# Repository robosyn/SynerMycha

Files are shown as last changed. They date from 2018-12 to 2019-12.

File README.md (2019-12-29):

# SynerMycha

Projekt micromouse'a

## BOM

|Qty|Value|Device|Package|Parts|Description|
|---|-----|---|---|-----|---|
|3|Blue|LEDCHIP-LED0603|CHIP-LED0603|LED1,LED2,LED3||
|1|Red|LEDCHIPLED_0603|CHIPLED_0603|LED5||
|1||PINHD-1X2|1X02|POWER||
|1||PINHD-1X5|1X05|JP3||
|1||PINHD-2X3|2X03|JP1||
|1||SPDT-PTH-11.6X4.0MM|SPDT_PTH_11.6X4.0MM|S1||
|12|100nF|CAPACITOR_SMD_0603|C0603K|C5,C6,C16,C18,C19,C21,C23,C24,C27,C29,C31,C36||
|1|100nF|CPOL-EUSMCA|SMC_A|C1||
|7|10k|RESISTOR_SMD_0603|R0603|R8,R15,R16,R25,R26,R27,R28||
|1|16Mhz|CRYSTAL_SMALL";|Y1|12.0MHzCrystal||
|2|18pF|CAPACITOR_SMD_0603|C0603K|C8,C9||
|2|1k|R-EU_R0603|R0603|R13,R14||
|5|1k|RESISTOR_SMD_0603|R0603|R2,R3,R4,R5,R7||
|1|270|RESISTOR_SMD_0603|R0603|R6||
|7|2k2|RESISTOR_SMD_0603|R0603|R1,R9,R10,R11,R12,R23,R24||
|3|330|R-EU_R0402|R0402|R17,R18,R19||
|5|33uF|CPOL-EUC|PANASONIC_C|C3,C4,C7,C32,C34||
|2|ACS711|ACS712|SOIC127P600X175-8N|IC3,IC4||
|5|ADAFRUIT-VCNL4010|ADAFRUIT-VCNL4010|ADAFRUIT-VCNL4010|U$7,U$8,U$9,U$10,U$11||
|5|BC847|BC847|SOT23|T1,T2,T3,T4,T5||
|1|MICROMATCH-6|MICROMATCH-6|MICROMATCH-6|PROG-SWDIO||
|1|SPST-SMD-6.2MM|SPST-SMD-6.2MM|SPST_SMD_6.2MM|S2||
|2|AS5040|AS5040|AS5040|U$13,U$14||
|1|STM32F411RCT6|STM32F411RCT6|LQFP64|IC7||
|1|SWS004|SWS004|SMS-004|S3||
|2|TLE9201SG|TLE9201SG|PG-DSO-12-9|IC5,IC6||
|1|3V3|V_REG_317-DPACK|V-REG_DPACK|U2||
|2|N20BT06100:1|N20BT06100:1||||
|2|RW2isolarbotics|RW2isolarbotics||||
|2|300mAh|LiPol,Dualsky||||

## Linki do niektórych części

| Nazwa |kamami ID |cena (botland) |botland |electropark |tme |
| ---|:-----:|:---:|:---:|:---:|:--:|
| N20 BT06 | 562730 | 19.9zł| https://botland.com.pl/pl/silniki-micro-n20-seria-mp-medium-power/12545-silnik-n20-bt05-micro-501-625rpm-12v.html | tylko oryginalne |  tylko oryginalne pololu|
| RW2i solarbotics | 195993 | 24.9zł| https://botland.com.pl/pl/kola-z-oponami/24-kolo-solarbotics-rw2i-mocowane-wewnetrznie.html | chwilowo niedostpne | brak|
| lipol 300mah dualsky  | brak | 22.5zł| https://botland.com.pl/pl/akumulatory-li-pol/7876-pakiet-li-pol-dualsky-300mah-30c-2s-74v-6941047107403.html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 | wycofany | brak |
| stm32f411 | 233365 | brak  | chwilowo niedostępnu| 27.65 zł|https://www.tme.eu/pl/details/stm32f411rct6/mikrokontrolery-st/stmicroelectronics/|
| TLE9201 | brak | brak  | brak |13.93zł| https://www.tme.eu/pl/details/tle9201sgauma1/drivery-silnikowe-i-pwm/infineon-technologies/ |
| VCNL4010 | brak | 44zł  | https://botland.com.pl/pl/cyfrowe-czujniki-odleglosci/4969-adafruit-vcnl4010-czujnik-odleglosci-i-swiatla-20cm-i2c.html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| |tylko chip bez płytki na specjalne zamówienie |

~ oferta: 
~ 35zł https://www.elfadistrelec.pl/pl/czujnik-zblizeniowy-swiatla-vcnl4010-adafruit-466/p/30139237
plus ~50 za przesyłke
TLE9210 dostępne w labie

### CADLAB 

View this project on [CADLAB.io](https://cadlab.io/project/1503).

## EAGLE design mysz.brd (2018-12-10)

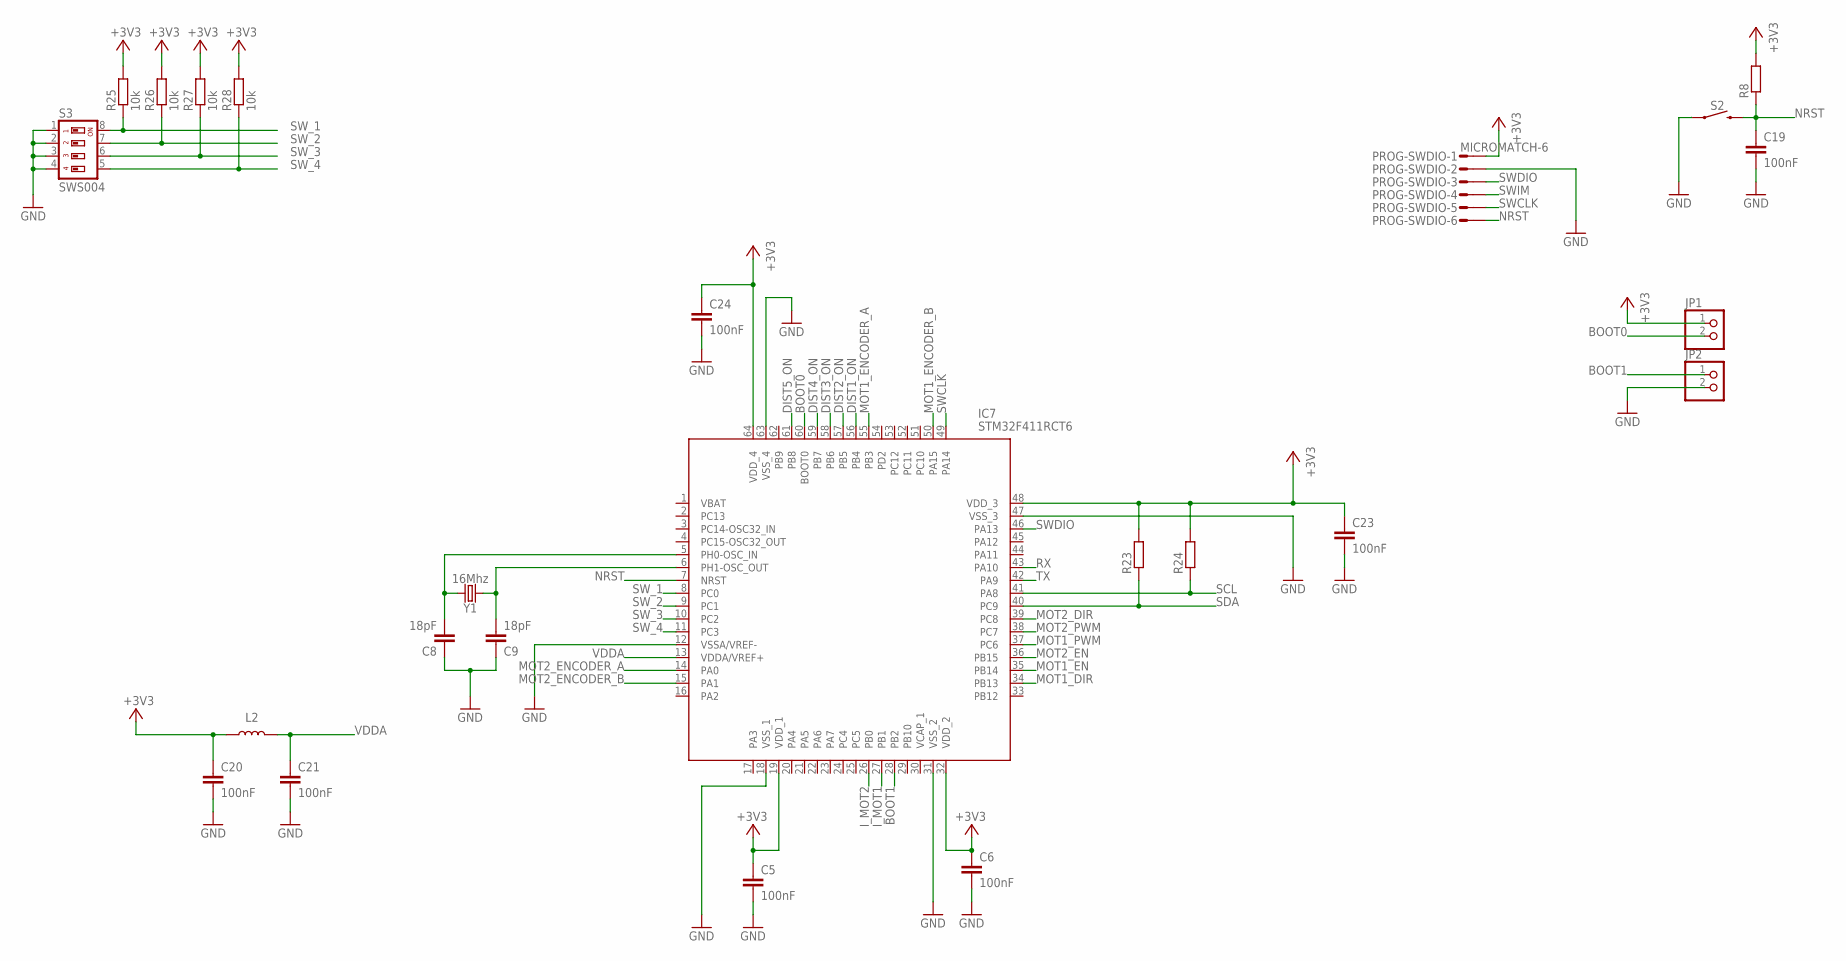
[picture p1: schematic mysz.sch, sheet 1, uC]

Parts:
C5, C6, C19, C20, C21, C23, C24: 100nF; C0603K
C8, C9: 18pF; C0603K
IC7: STM32F411RCT6; QFP50P1200X1200X160-64N
JP1, JP2: PINHD-1X2; 1X02
L2: INDUCTOR-0603; R0603
PROG-SWDIO: MICROMATCH-6
R8, R23, R24: RESISTOR_SMD_0603; R0603
R25, R26, R27, R28: 10k; R0603
S2: MOMENTARY-SWITCH-SPST-SMD-6.2MM_TALL; TACTILE_SWITCH_SMD_6.2MM_TALL
S3: SWS004; SMS-004
Y1: 16Mhz; CRYSTAL-SMD-5X3.2-4PAD

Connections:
+3V3: C5.1, C6.1, C20.1, C23.1, C24.1, IC7.19 (VDD_1), IC7.32 (VDD_2), IC7.48 (VDD_3), IC7.64 (VDD_4), JP1.1, L2.1, PROG-SWDIO.1, R8.2, R23.2, R24.2, R25.2, R26.2, R27.2, R28.2; also elsewhere on the board
BOOT0: IC7.60 (BOOT0), JP1.2
BOOT1: IC7.28 (PB2), JP2.1
DIST1_ON: IC7.56 (PB4); also elsewhere on the board
DIST2_ON: IC7.57 (PB5); also elsewhere on the board
DIST3_ON: IC7.58 (PB6); also elsewhere on the board
DIST4_ON: IC7.59 (PB7); also elsewhere on the board
DIST5_ON: IC7.61 (PB8); also elsewhere on the board
GND: C5.2, C6.2, C8.1, C9.1, C19.2, C20.2, C21.2, C23.2, C24.2, IC7.12 (VSSA/VREF-), IC7.18 (VSS_1), IC7.31 (VSS_2), IC7.47 (VSS_3), IC7.63 (VSS_4), JP2.2, PROG-SWDIO.2, S2.A1 (1), S2.A2 (1), S3.1, S3.2, S3.3, S3.4; also elsewhere on the board
I_MOT1: IC7.27 (PB1); also elsewhere on the board
I_MOT2: IC7.26 (PB0); also elsewhere on the board
MOT1_DIR: IC7.34 (PB13); also elsewhere on the board
MOT1_EN: IC7.35 (PB14); also elsewhere on the board
MOT1_ENCODER_A: IC7.55 (PB3); also elsewhere on the board
MOT1_ENCODER_B: IC7.50 (PA15); also elsewhere on the board
MOT1_PWM: IC7.37 (PC6); also elsewhere on the board
MOT2_DIR: IC7.39 (PC8); also elsewhere on the board
MOT2_EN: IC7.36 (PB15); also elsewhere on the board
MOT2_ENCODER_A: IC7.14 (PA0); also elsewhere on the board
MOT2_ENCODER_B: IC7.15 (PA1); also elsewhere on the board
MOT2_PWM: IC7.38 (PC7); also elsewhere on the board
NRST: C19.1, IC7.7 (NRST), PROG-SWDIO.6, R8.1, S2.B1 (2), S2.B2 (2)
RCC_OSC_IN: C8.2, IC7.5 (PH0-OSC_IN), Y1.3 (2)
RCC_OSC_OUT: C9.2, IC7.6 (PH1-OSC_OUT), Y1.1
RX: IC7.43 (PA10)
SCL: IC7.41 (PA8), R24.1; also elsewhere on the board
SDA: IC7.40 (PC9), R23.1; also elsewhere on the board
SWCLK: IC7.49 (PA14), PROG-SWDIO.5
SWDIO: IC7.46 (PA13), PROG-SWDIO.3
SWIM: PROG-SWDIO.4
SW_1: IC7.8 (PC0), R25.1, S3.8
SW_2: IC7.9 (PC1), R26.1, S3.7
SW_3: IC7.10 (PC2), R27.1, S3.6
SW_4: IC7.11 (PC3), R28.1, S3.5
TX: IC7.42 (PA9)
VDDA: C21.1, IC7.13 (VDDA/VREF+), L2.2

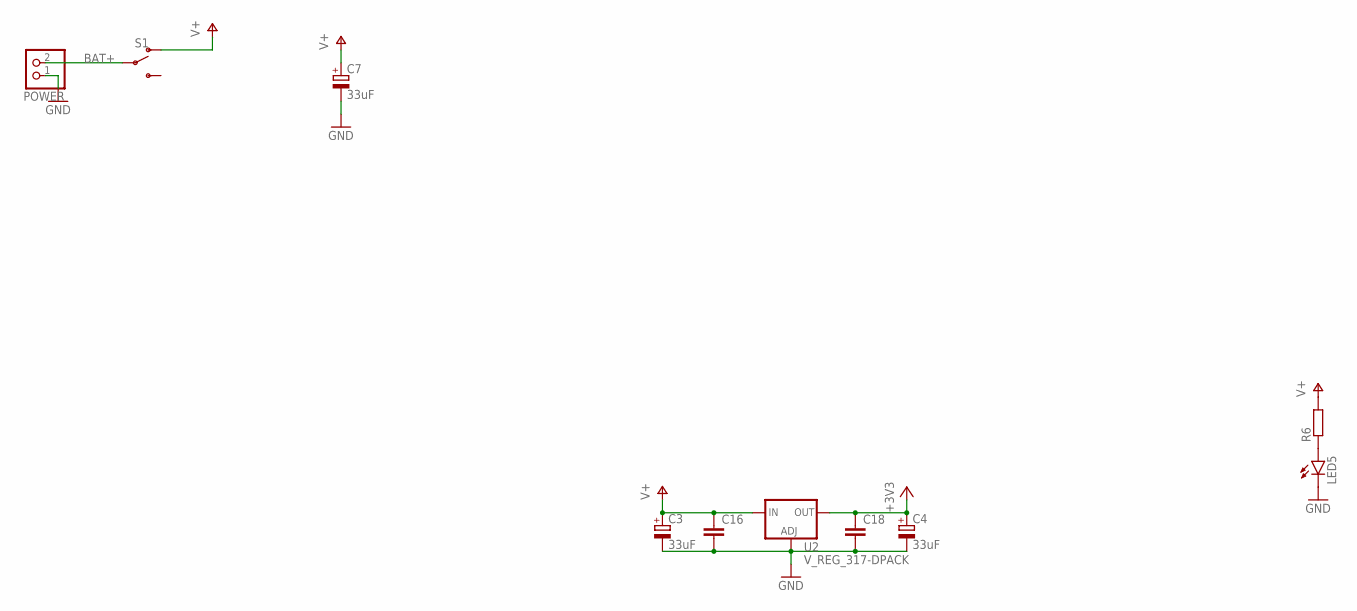
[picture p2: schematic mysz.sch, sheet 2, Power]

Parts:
C3, C4, C7: 33uF; PANASONIC_C
C16, C18: CAPACITOR_SMD_0603; C0603K
LED5: LEDCHIPLED_0603; CHIPLED_0603
POWER: PINHD-1X2; 1X02
R6: RESISTOR_SMD_0603; R0603
S1: SWITCH-SPDT-PTH-11.6X4.0MM; SWITCH_SPDT_PTH_11.6X4.0MM
U2: V_REG_317-DPACK; V-REG_DPACK

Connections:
+3V3: C4.+, C18.1, U2.4 (OUT); also elsewhere on the board
BAT+: POWER.2, S1.2
GND: C3.-, C4.-, C7.-, C16.2, C18.2, LED5.C, POWER.1, U2.1 (ADJ); also elsewhere on the board
unnamed: LED5.A, R6.1
V+: C3.+, C7.+, C16.1, R6.2, S1.1 (O), U2.3 (IN); also elsewhere on the board

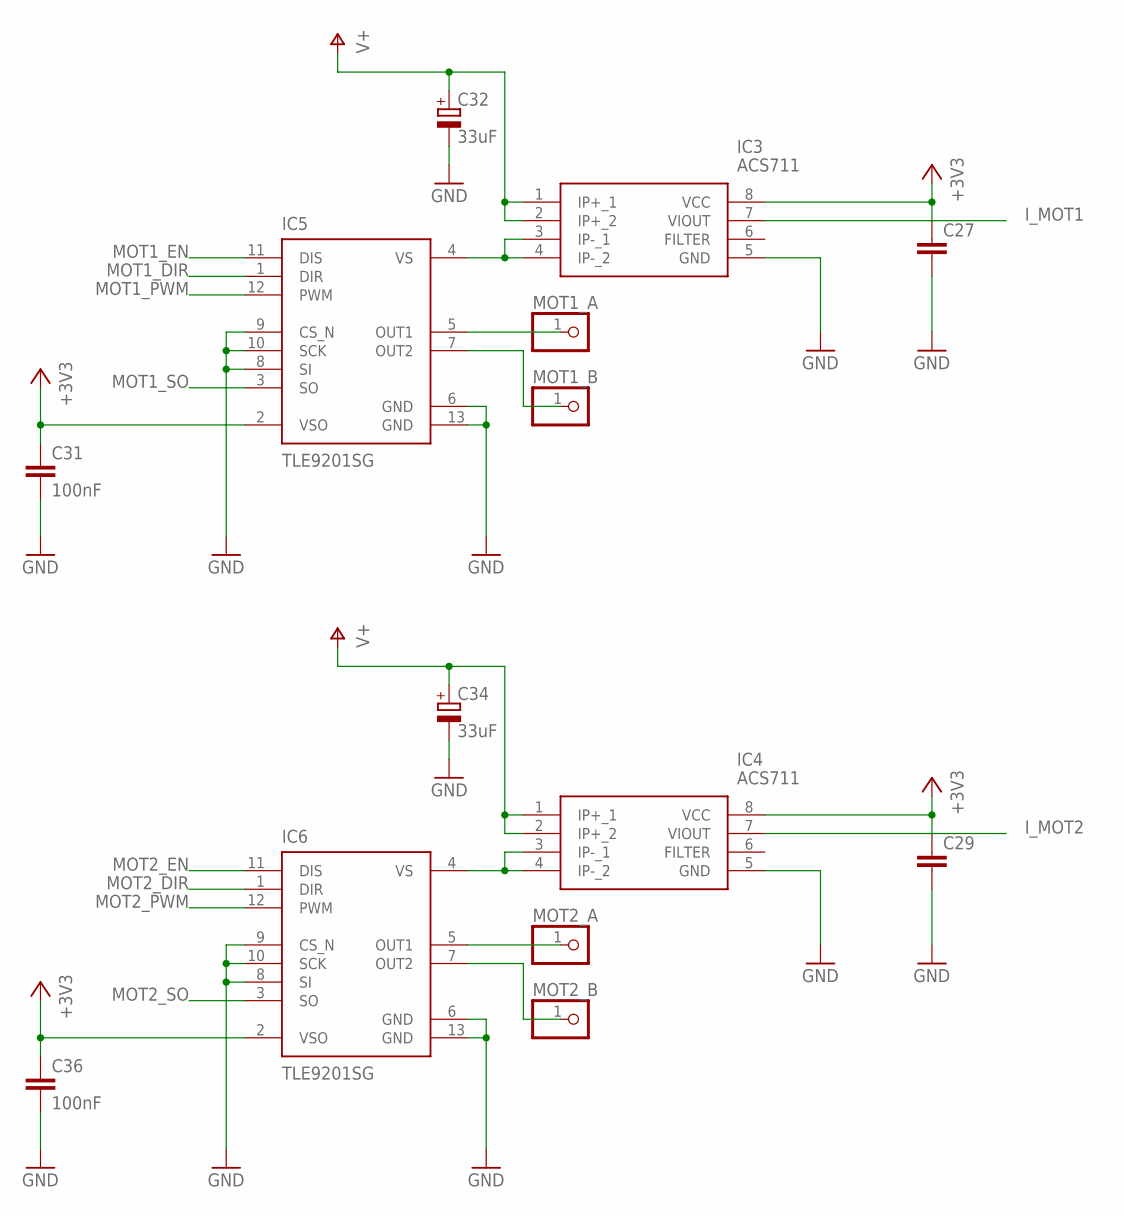
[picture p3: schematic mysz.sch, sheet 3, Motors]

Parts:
C27, C29: CAPACITOR_SMD_0603; C0603K
C31, C36: 100nF; C0603K
C32, C34: 33uF; PANASONIC_C
IC3, IC4: ACS711; SOIC127P600X175-8N
IC5, IC6: TLE9201SG; PG-DSO-12-9
MOT1_A, MOT1_B, MOT2_A, MOT2_B: PINHD-1X1; 1X01

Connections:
+3V3: C27.1, C29.1, C31.1, C36.1, IC3.8 (VCC), IC4.8 (VCC), IC5.2 (VSO), IC6.2 (VSO); also elsewhere on the board
GND: C27.2, C29.2, C31.2, C32.-, C34.-, C36.2, IC3.5 (GND), IC4.5 (GND), IC5.6 (GND), IC5.8 (SI), IC5.9 (CS_N), IC5.10 (SCK), IC5.13 (GND), IC6.6 (GND), IC6.8 (SI), IC6.9 (CS_N), IC6.10 (SCK), IC6.13 (GND); also elsewhere on the board
I_MOT1: IC3.7 (VIOUT); also elsewhere on the board
I_MOT2: IC4.7 (VIOUT); also elsewhere on the board
MOT1_A: IC5.5 (OUT1), MOT1_A.1
MOT1_B: IC5.7 (OUT2), MOT1_B.1
MOT1_DIR: IC5.1 (DIR); also elsewhere on the board
MOT1_EN: IC5.11 (DIS); also elsewhere on the board
MOT1_PWM: IC5.12 (PWM); also elsewhere on the board
MOT1_SO: IC5.3 (SO)
MOT1_VS: IC3.3 (IP-_1), IC3.4 (IP-_2), IC5.4 (VS)
MOT2_A: IC6.5 (OUT1), MOT2_A.1
MOT2_B: IC6.7 (OUT2), MOT2_B.1
MOT2_DIR: IC6.1 (DIR); also elsewhere on the board
MOT2_EN: IC6.11 (DIS); also elsewhere on the board
MOT2_PWM: IC6.12 (PWM); also elsewhere on the board
MOT2_SO: IC6.3 (SO)
MOT2_VS: IC4.3 (IP-_1), IC4.4 (IP-_2), IC6.4 (VS)
V+: C32.+, C34.+, IC3.1 (IP+_1), IC3.2 (IP+_2), IC4.1 (IP+_1), IC4.2 (IP+_2); also elsewhere on the board

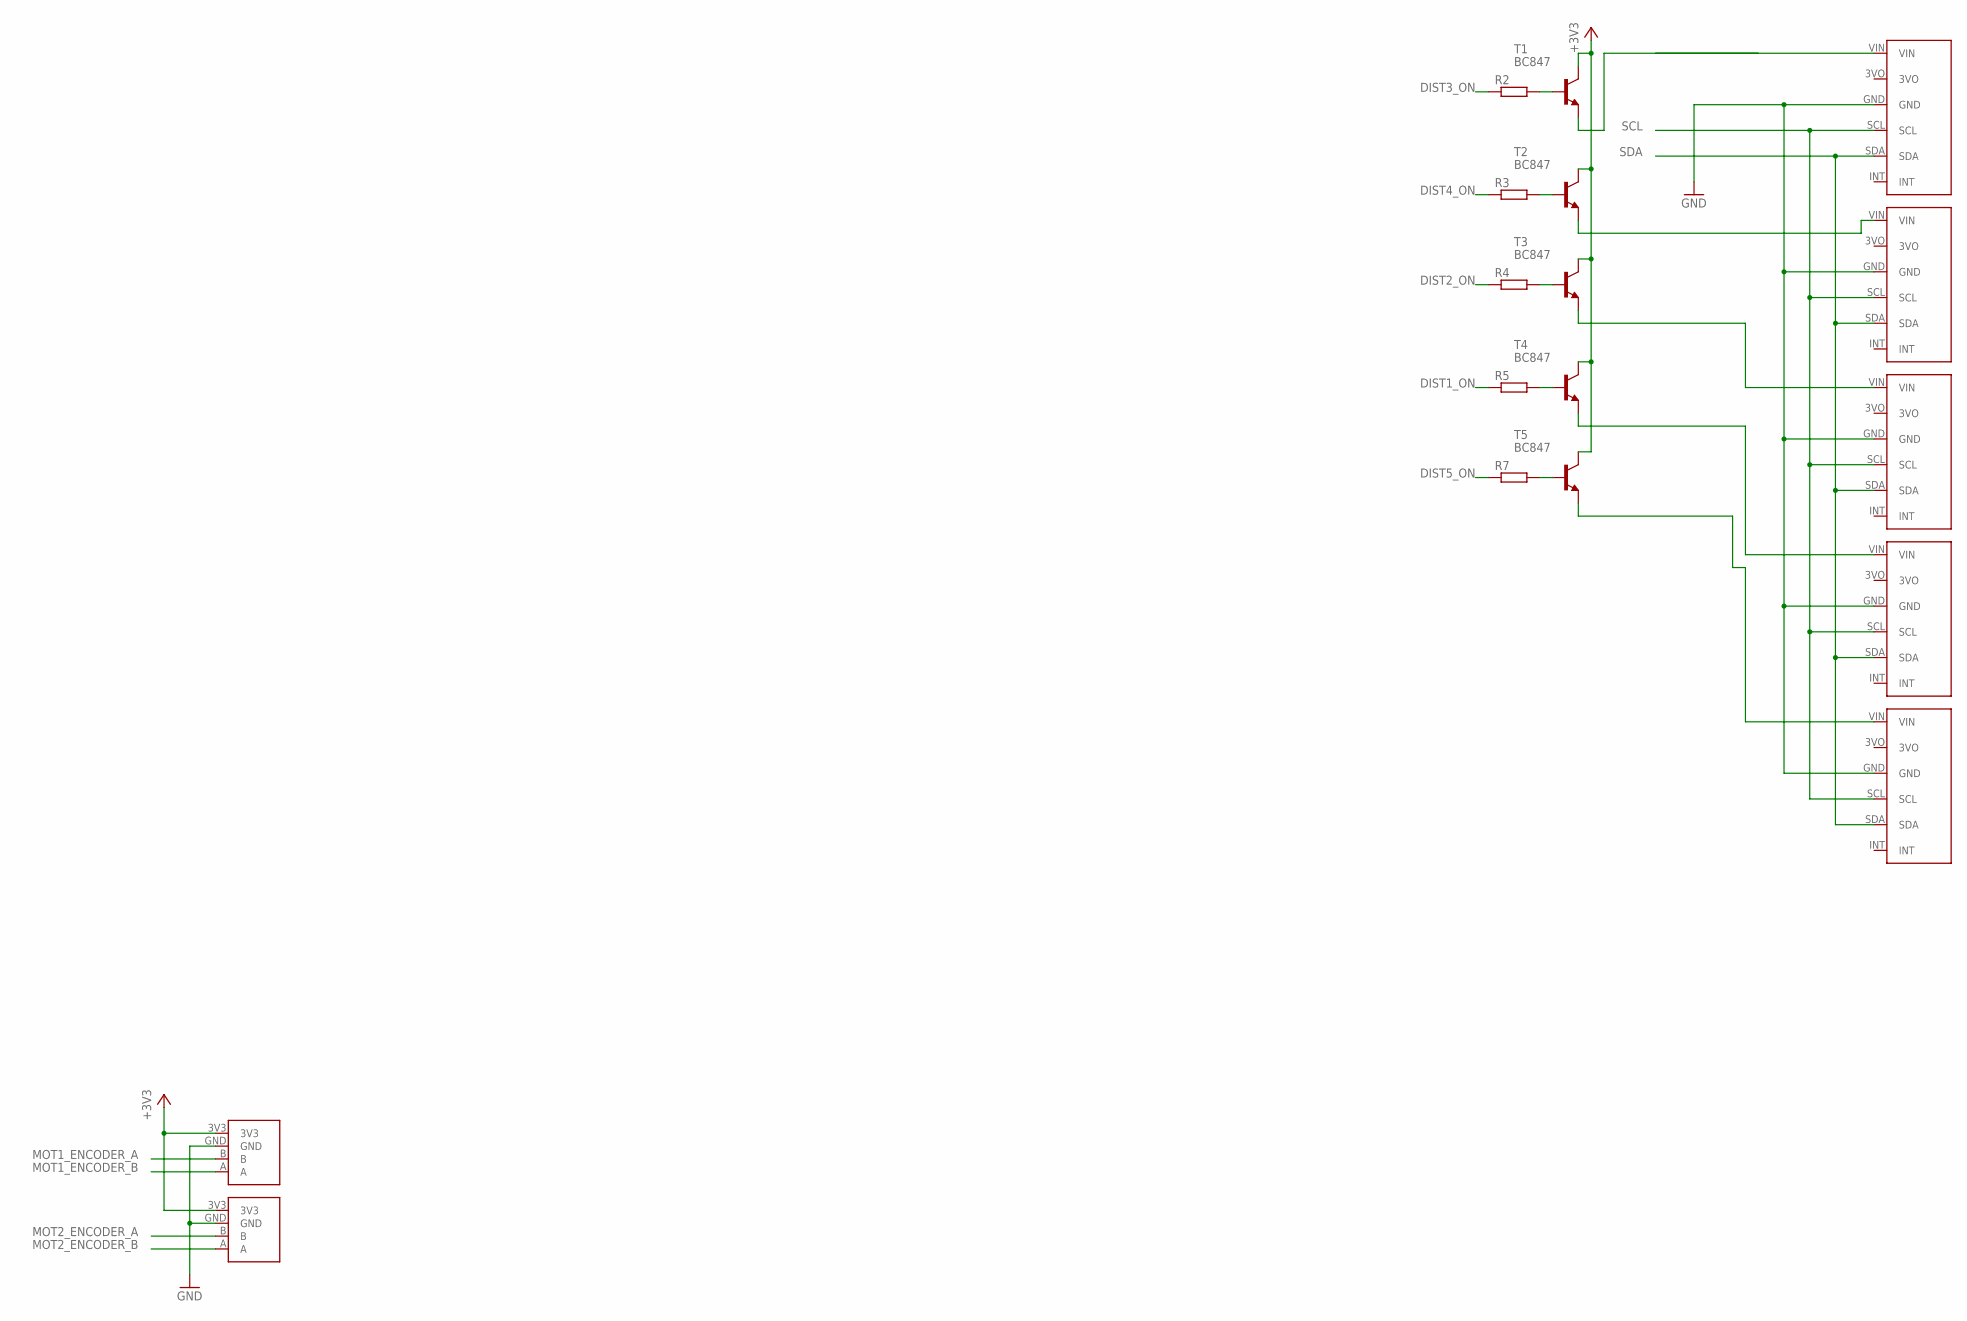
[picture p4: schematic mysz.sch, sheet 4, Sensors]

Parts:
R2, R3, R4, R5, R7: RESISTOR_SMD_0603; R0603
T1, T2, T3, T4, T5: BC847; SOT23
U$7, U$8, U$9, U$10, U$11: ADAFRUIT-VCNL4010
U$13, U$14: PRIV-AS5040

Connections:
+3V3: T1.3 (C), T2.3 (C), T3.3 (C), T4.3 (C), T5.3 (C), U$13.3V3, U$14.3V3; also elsewhere on the board
DIST1_ON: R5.1; also elsewhere on the board
DIST2_ON: R4.1; also elsewhere on the board
DIST3_ON: R2.1; also elsewhere on the board
DIST4_ON: R3.1; also elsewhere on the board
DIST5_ON: R7.1; also elsewhere on the board
GND: U$7.GND, U$8.GND, U$9.GND, U$10.GND, U$11.GND, U$13.GND, U$14.GND; also elsewhere on the board
MOT1_ENCODER_A: U$14.B; also elsewhere on the board
MOT1_ENCODER_B: U$14.A; also elsewhere on the board
MOT2_ENCODER_A: U$13.B; also elsewhere on the board
MOT2_ENCODER_B: U$13.A; also elsewhere on the board
unnamed: R2.2, T1.1 (B)
unnamed: R3.2, T2.1 (B)
unnamed: R4.2, T3.1 (B)
unnamed: R5.2, T4.1 (B)
unnamed: R7.2, T5.1 (B)
unnamed: T2.2 (E), U$8.VIN
unnamed: T1.2 (E), U$7.VIN
unnamed: T3.2 (E), U$9.VIN
unnamed: T4.2 (E), U$10.VIN
unnamed: T5.2 (E), U$11.VIN
SCL: U$7.SCL, U$8.SCL, U$9.SCL, U$10.SCL, U$11.SCL; also elsewhere on the board
SDA: U$7.SDA, U$8.SDA, U$9.SDA, U$10.SDA, U$11.SDA; also elsewhere on the board

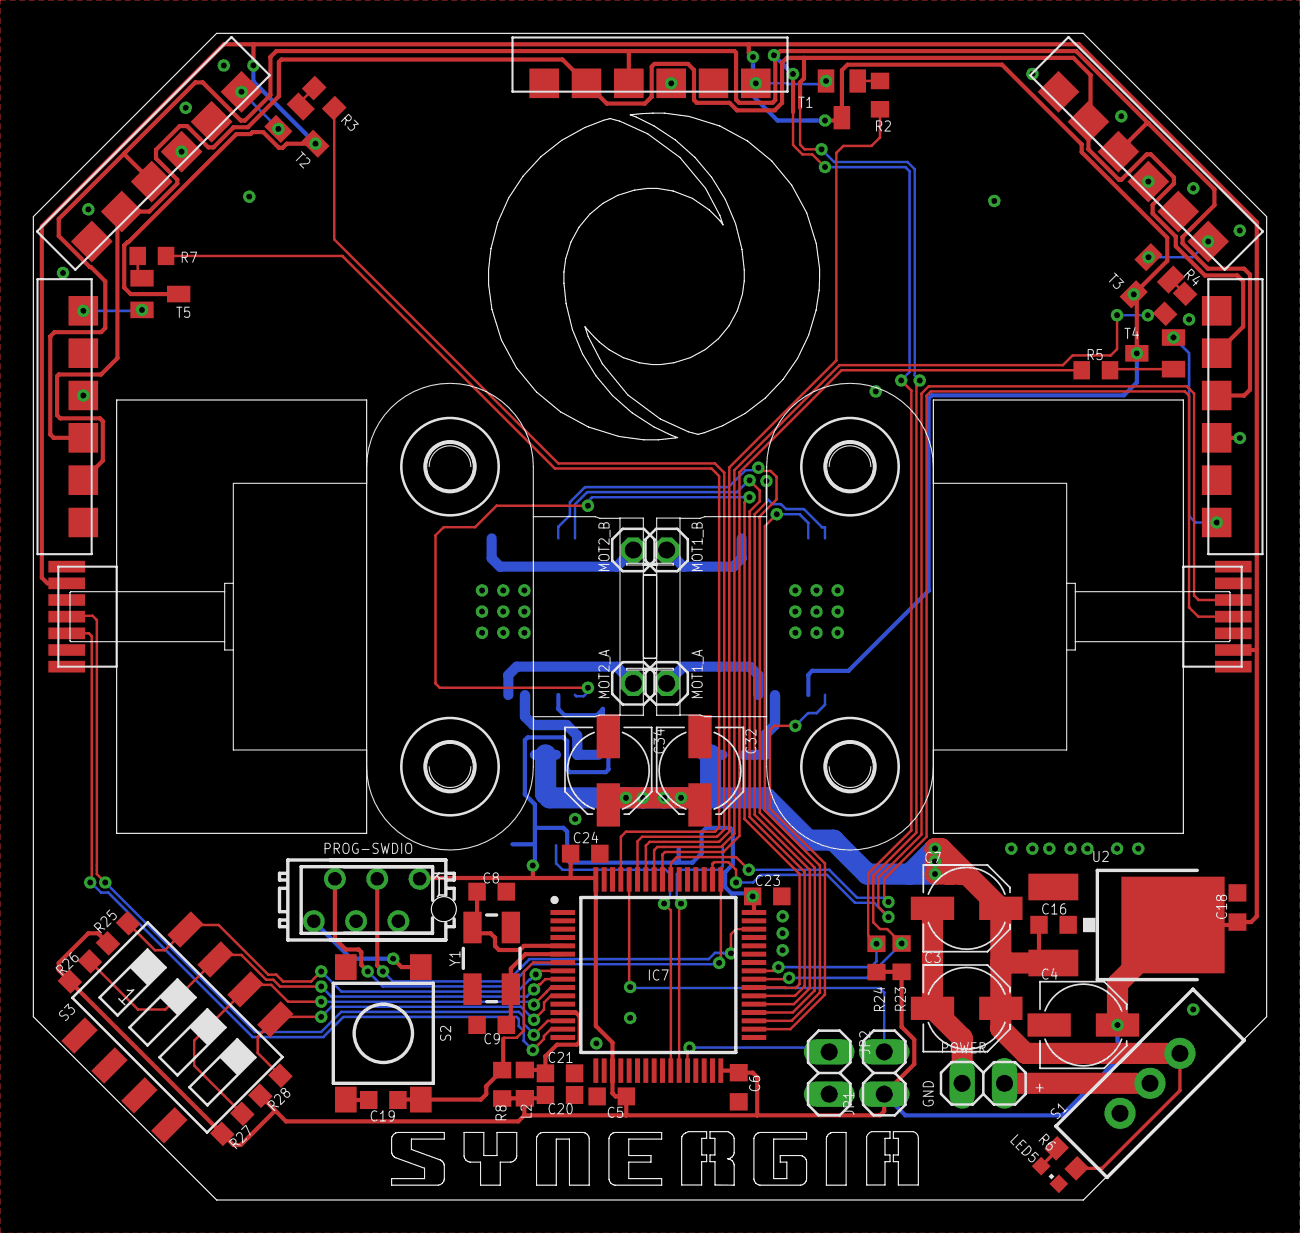
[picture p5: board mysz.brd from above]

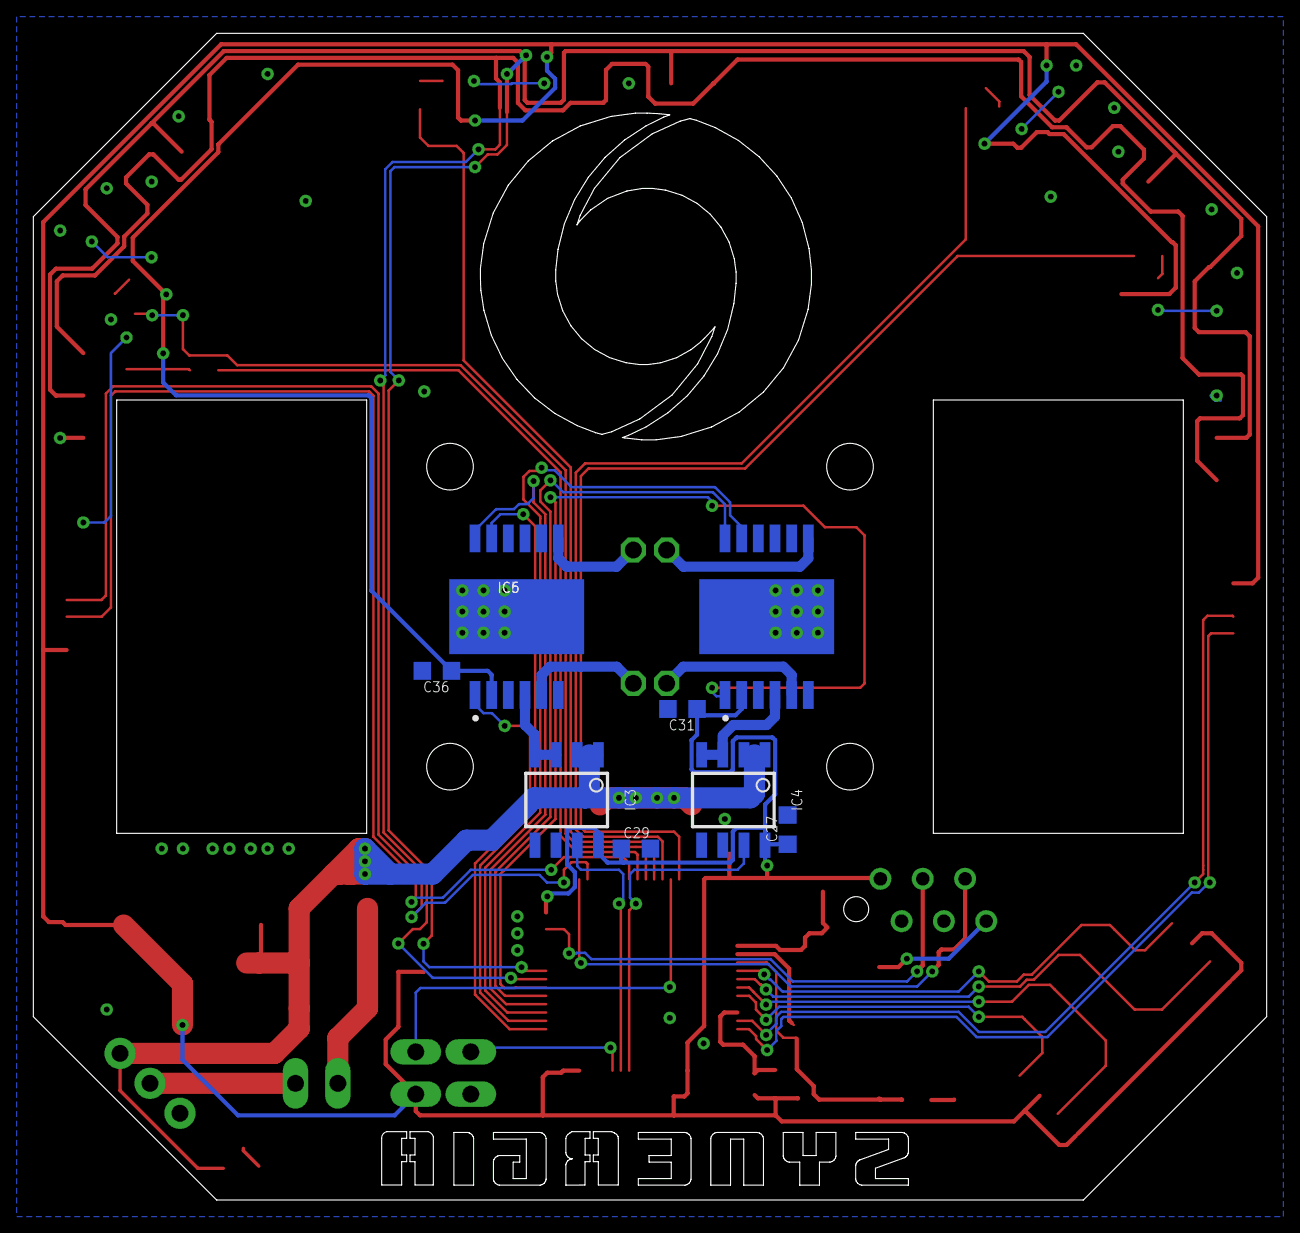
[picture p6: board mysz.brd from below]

Board: 2 copper layers, 74.0 x 70.0 mm, 71 parts (8 on the bottom side), 52 nets.

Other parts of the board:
U$1, U$2: POLOLU_SINGLE_SHAFT
U$3, U$4, U$5, U$6: 2,8

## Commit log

2018-11-01 Old design copy
    [mysz.sch, mysz_druk.brd]
2018-11-26 Added all planned sensors to schematic
    [mysz.brd, mysz.sch, mysz_druk.brd]
2018-11-28 Getting smaller
    [mysz.brd, mysz.sch]
2018-12-10 Finished wiring
    [mysz.brd, mysz.sch]

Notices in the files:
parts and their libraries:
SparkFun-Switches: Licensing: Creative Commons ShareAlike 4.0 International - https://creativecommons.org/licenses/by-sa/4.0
